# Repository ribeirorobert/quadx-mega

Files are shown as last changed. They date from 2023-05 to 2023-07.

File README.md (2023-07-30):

# Quadx-Mega: Quadricoptero com Arduino (Quadcopter with Arduino)
QuadX-Mega é um quadricoptero desenvolvido com um microcontrolador Arduino Mega Pro mini. O objetivo desse repositório é apresentar de forma simples o hardware e software necessários para a construção de um drone caseiro. A descrição desse projeto tem como base o trabalho de Joop Brokking e totalmente sem fins lucrativos.

Esse projeto destinado a pessoas que gostam de programação, eletrônica, drones, hobbistas e entusiasta de aeromodelos e aviação. Em caso de dúvidas podem entrar em contato direto pelo GitHub ou através do e-mail: robertribeiro100@gmail.com. 

Site do Joop Brokking: http://www.brokking.net/.

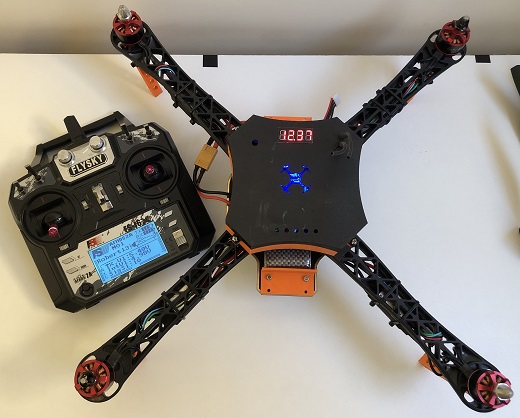
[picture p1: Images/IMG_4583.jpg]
|  | 
|:--:| 
| **Fig. 1** *QuadX-Mega* |

<!-- ![image](https://github.com/ribeirorobert/quadx-mega/edit/feature/altitude-hold/Images/IMG_4565.jpg) -->

# Hardware
A seguir é listado os componentes e peças utilizadas para a construção do quadricoptero. Entretanto, fica a critério e responsabilidade de quem está construindo escolher os itens que irão compor o projeto. Ainda, reforço que nem todos esses componentes são os melhores e mais indicados do mercado, não sendo objetivo construir um drone com melhor preço, com voos a longas distâncias tão pouco a análise da capacidade de carga e duração de voo.

* 1x Frame F450.
* 4x Motor Brushless ReadyToSky 2212 920KV.
* 4x ESC de 30A SimonK.
* 4x Hélice 10x4.5 (2cw e 2 ccw).
* 1x Bateria de Lipo 3S ou 4S com capacidade maior ou igual a 3000mAh. 
* 1x Carregador de bateria Lipo.
* 1x Indicador e alarme de bateria (opcional)
* 1x Radio controle com no mínimo 6 canais. 
* 1x Arduino Mega Pro mini.
* 1x Módulo MPU6050 -> Acelerômetro e Giroscópio 
* 1x Módulo HMC5883L -> Magnetômetro (opcional)
* 1x Módulo MS5611 -> Sensor de pressão barométrica (opcional)
* 1x Módulo GPS NEO 6MV2 (opcional)
* 1x Módulo de comunicação RF Xbee, Lora, NRF24L01 ou APC220 (opcional)
* 1x Buzzer 5V
* 1x LED vermelho
* 1x LED verde
* 1x LED amarelo
* 1x Balanceador de hélice
* 1x Cinta para fixar bateria (opcional)

Observações: 
1. Os motores utilizados possuem furação de fixação em conformidade com o frame. Se optar por utilizar outro conjunto, verifique se a fixação dos motores é coerente com a do frame. 
2. KV: constante de velocidade (para cada 1V de tensão de alimentação há um incremento teórico da velocidade de 920 rpm).
3. Os ESC's utilizados suportam baterias de 2S a 4S.
4. A escolha da hélice tem relação com o tipo de drone que se deseja construir. Algumas são para aplicações onde a prioridade é velocidade. Por outro lado há hélices que são para aplicações onde o peso é o mais importante. Hélices do modelo 10x4.5 são muito comuns e estão no meio termo entre velocidade-peso.
5. O indicador de alarme da bateria é muito útil principalmente para quem está aprendendo a controlar drones/aeromodelos e aqueles que ainda não possuem telemetria integrado. É emitido um alarme sonoro quando a tensão da bateria chega a tensão de limiar pré-definida. O QuadX-Mega possui uma lógica para emitir alarme quando a tensão da bateria atingir 10.7V. Em geral, é definido uma tensão de descarga mínima para cada célula da bateria para garantir sua vida útil. Descargas profundas reduzem a vida útil da bateria. Para o QuadX-Mega a tensão de descarga mínima por célula é de 3,5V com acréscimo de 0,2V como margem de segurança. Em situações em que o quadricoptero esteja a uma distância considerável do operador é aconselhável ter um pouco mais de energia para ganrantir o retorno de forma segura.
6. Em geral um rádio de apenas 4 canais (Roll-CH1, Pitch-CH2, Yaw-CH4 e Throttle-CH3) é suficiente para controlar um drone simples. Entretando, quanto maior o número de canais mais configurações e comandos podem ser adicionados.
7. A escolha do Arduino Mega Pro mini é em função da quantidade de I/Os e tamanho. Outros microcontroladores como Arduino UNO, Arduino Nano, ESP32 ou STM32F103 poderiam ser utilizados tomando os devidos cuidados e modificações pertinentes a cada sistema.
8. O módulo MPU6050 foi utilizado devido a sua qualidade. Existem diversos modelos de acelerômetros disponível no mercado e alguns com mais graus de liberdade (DOFs) como de exemplo o MPU9250 que é um módulo com 9DOFs (acelerômetro, giroscópio e bússola).
9. A PCI (Placa de Circuito Impresso) projetada permite a utilização de diversos sensores e módulos. São eles: MPU6050, MPU9250, BMP180 ou BMP085, HMC5883L, MS5611, GPS NEO-6MV2 e módulos para telemetria via comunicação serial.

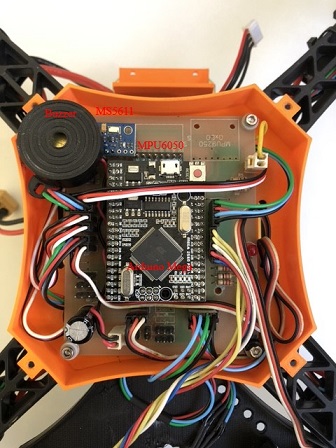
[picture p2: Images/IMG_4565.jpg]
|    | 
|:--:| 
| **Fig. 2** *Eletrônica do quadricoptero* |

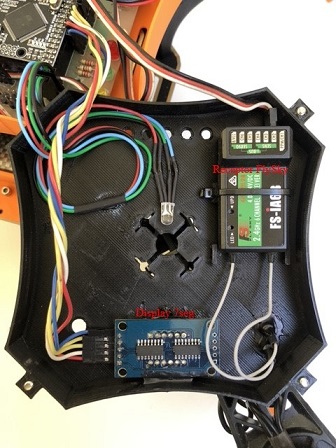
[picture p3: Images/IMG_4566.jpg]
|    | 
|:--:| 
| **Fig. 3** *Eletrônica do quadricoptero* |

O esquemático, lista de componentes e o arquivo Gerber da PCI estão na [pasta PCI](https://github.com/ribeirorobert/quadx-mega/tree/main/PCI) do repositório. 

# Arquivos .STL (STL Files)
Os arquivos .STL utilizados no projeto podem ser acessados diretamente na pasta [STL_files](https://github.com/ribeirorobert/quadx-mega/tree/main/STL_files) do repositório. São eles:
* Skid do trem de pouso.
* Suporte para bateria.
* Case principal.

Observações: 
Foram utilizados peças de fabricação em impressora 3D, mas a confecção desses itens não é obrigatória. Assim, fica a critério do hobbista posicionar certos itens. 

1. Na maioria dos casos o frame do F450 acompanha o skid do trem de pouso principal. Porém, o drone fica um pouco alto (na minha opnião) e em muitas situações fica instável no pouso e decolagem. E como resultado muitas hélices acabam quebrando nessas situações. 
2. A cinta para fixar a bateria é uma opção alternativa. 
3. A case principal foi projetada com objetivo de ser a menor e mais leve possível garantindo a proteção dos componentes da PCI.  

# Software
O código foi desenvolvido em C++ no VScode. Para realizar o download click no botão "<>Code" em verde -> Download ZIP. Ou se preferir basta usar o comando de clone através do git: git clone https://github.com/ribeirorobert/quadx-mega.git que será criado uma cópia do repositório.

O código tem tamanho relativamente grande. Alguns rotinas e funções importantes serão descritas a seguir.

### Defines
Os defines são utilizados para deixar o código mais limpo e organizado além de possibilidar uma maior dinâmica do que está ou não habilitado (flags). Algumas constantes foram definidas com base no datasheet e dados técnicos dos sensores, por outro lado algumas contantes foram obtidas em referência ao trabalho de Joop Brokking ou de forma empírica. Ao mudar alguma constante ou flag tenha certeza do que está fazendo.

As flags a seguir têm função de: habilitar a função de telemetria (se utilizada), habilitar a portal serial do Arduino (para debug), habilitar a rotina com diversas telas de debug, habilitar funções do sensor BMP180 ou MS5611, habilitar a rotina de Fail Safe se implementada, respectivamente. 

```
#define TELEMETRY_ENABLE    0
#define SERIAL_ENABLE       0
#define PRINTF_ENABLE       0
#define BMP180_ENABLE       0
#define MS5611_ENABLE       1
#define FAIL_SAFE           0
```

Já as flags a seguir tem função de habilitar o debug de verificação dos sensores na inicialização do quadricoptero, debug da EEPROM, debug da calibração da IMU, debug da calibração dos ESC's.

```
#define DEBUG_STATUS        0
#define DEBUG_EEPROM        0
#define DEBUG_MPU           0
#define DEBUG_ESC           0
```

### Variáveis
As variáveis em sua maioria são para armazenar os dados dos sensores, controle PID dos ângulo de rolagem (Roll), arfagem (Pitch) e guinada (Yaw), tensão da bateria e status do quadricoptero de modo geral.

### Setup
O setup é função responsável por definir quais pinos do microcontrolador serão definidos como entrada ou saída, inicializar as portas de comunicação Serial e I2C, configurar os pinos de PWM (Pulse Width Modulation) dos ESC's, verificar se os sensores habilitados estão respondendo corretamente e atualizar os timers utilizados no código.

### Loop
É a função principal do código e todas as demais rotinas serão chaveadas de maneira sequencial. É importante destacar que o loop "roda" a uma taxa de 250 Hz (4ms). Esse valor foi definido em conformidade com a frequência de operação dos ESC's. Assim, todas as demais rotinas de controle e leitura dos sensores estão sendo executadas nessa velocidade. Em alguns casos expecíficos como de exemplo da aquisição dos dados do sensor de pressão barométrica foram criados artifícios para escalonar essa taxa. As funções executadas dentro do loop são descritas a seguir.

1. acc_gyro_values(): Essa rotina é responsável por aquisitar os bytes do registradores do acelerômetro e giroscópio do sensor MPU6050 e ainda subtrair dos valores de calibração.

2. euler_angles(): É responsável por filtrar os dados obtidos na função anterior e computar os ângulos de Roll e Pitch através das Equações de Euler. 

Para mais informações visite: 
- https://www.youtube.com/watch?v=pQ24NtnaLl8 
- https://en.wikipedia.org/wiki/Euler_angles
- https://www.youtube.com/watch?v=5IkPWZjUQlw&t=17s
- https://www.youtube.com/watch?v=nCPEJTUYch8&t=616s
- https://www.youtube.com/watch?v=j-kE0AMEWy4&t=9s

3. read_radio_commands(): Essa função é responsável por interpretar alguns comandos combinados do rádio.
* Ligar/Desligar os motores

O status dos motores é divido em três categorias, são elas: LOCK, IDLE e FULL. No status de LOCK os motores permanecem desligados. Já no status de IDLE os motores são acionados em rotação mínima e por fim em FULL os motores podem assumir rotação entre minimo e máximo de acordo com a posição do stick de throttle do radio controle. O objetivo dessa implementação é evitar de modo não intencional os motores sejam acionados. Lembrando que motores brushless operam em rotações elevadas e com a hélice conectada tornam-se perigosos.

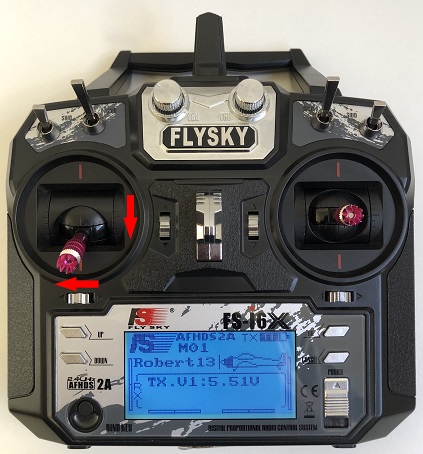
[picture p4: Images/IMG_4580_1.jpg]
|    | 
|:--:| 
| **Fig. 4** *Comando para ligar os motores* |

Seguindo a indicação das setas mostrado na Figura acima, uma primeira tentativa o status dos motores em LOCK muda para IDLE e um segunda tentativa os motores mudam para o status de FULL, ou seja, aceleração desbroqueada. Para desligar basta seguir a instrução da Figura 5.

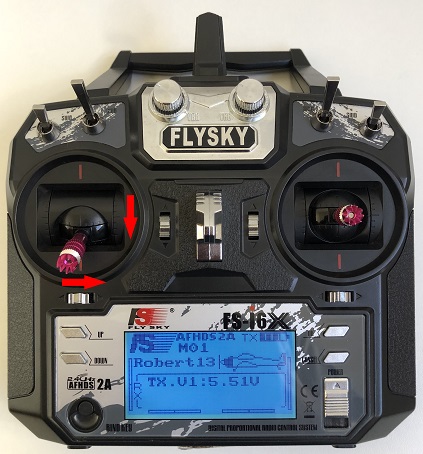
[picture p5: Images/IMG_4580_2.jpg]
|    | 
|:--:| 
| **Fig. 5** *Comando para desligar os motores* |

* Calibrar IMU -> Giroscópio

Da mesma forma para calibrar o giroscópio é preciso executar a instrução indicada em vermelho duas vezes. Caso queira cancelar a calibração, basta executar a indicação em azul (Figura 10).

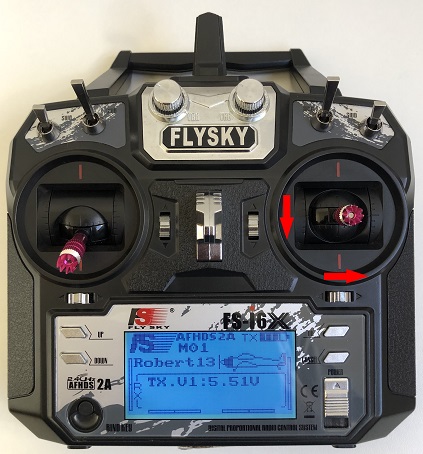
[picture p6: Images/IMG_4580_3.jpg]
|    | 
|:--:| 
| **Fig. 6** *Comando calibrar o giroscópio* |

* Calibrar IMU -> Acelerômetro

Para calibrar o acelerômetro é preciso executar a instrução indicada em vermelho duas vezes. Caso queira cancelar a calibração, basta executar a indicação em azul (Figura 10).

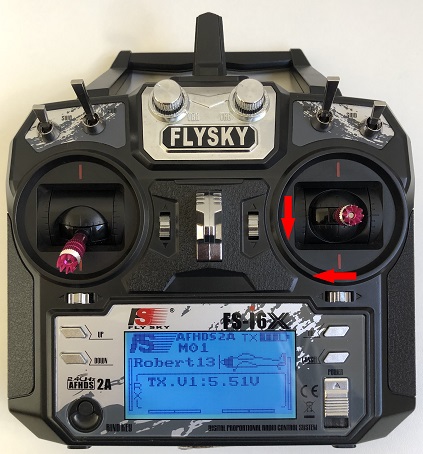
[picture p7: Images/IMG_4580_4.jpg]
|    | 
|:--:| 
| **Fig. 8** *Comando para calibrar o acelerômetro* |

* Calibrar os ESC's

Para calibrar os ESC's é preciso executar a instrução indicada em vermelho duas vezes (Figura 9). Caso queira cancelar a calibração, basta executar a indicação em azul (Figura 10). Porém, a calibração dos ESC's possui um terceira etapa da seguinte forma: 

- Desconecte a bateria e mova o stick do throttle para a posição máxima. 
- Conecte a bateria novamente e aguarde o beep dos motores.
- Mova o stick do throttle para a posição mínima e aguarde o beep dos motores novamente. 
    
Tudo executado corretamente basta realizar o comando para sair da calibração (Figura 10). Se esse comando não for executado ao fim da calibração, toda vez que o drone for ligado a rotina de calibração dos ESC's será executada primeiro.

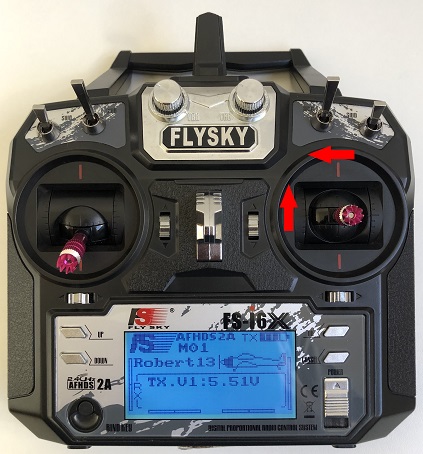
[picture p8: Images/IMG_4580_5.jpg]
|    | 
|:--:| 
| **Fig. 9** *Comando para calibrar os ESC's* |

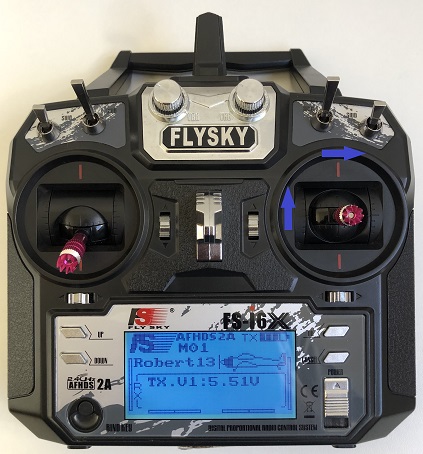
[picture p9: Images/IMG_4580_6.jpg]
|    | 
|:--:| 
| **Fig. 10** *Comando para cancelar* |

* Habilitar Altitude Hold (em desenvolvimento)

Quando habilitada a rotina de Altitude Hold possibilita com o que o quadricoptero permanace em uma altitude fixa usando como referência a pressão barométrica. Ao mover o stick de throttle essa referência de altitude é atualizada até que o stick retorne a posição central. 

Para mais informações da implementação visite: 
- https://www.youtube.com/watch?v=2BLb6qUKikI&t=702s

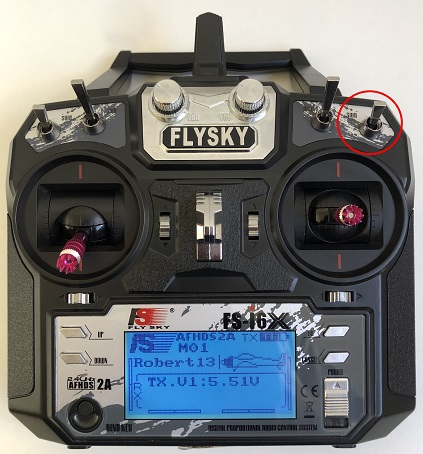
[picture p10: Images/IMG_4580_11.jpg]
|    | 
|:--:| 
| **Fig. 11** *Hibilitar o Altitude Hold* |

* Ligar/Desligar LEDs do frame

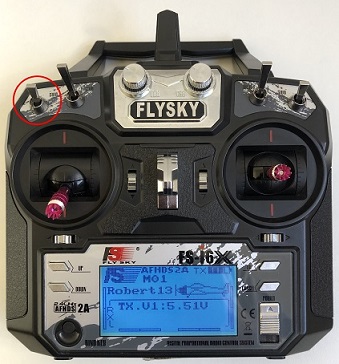
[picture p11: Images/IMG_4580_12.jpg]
|    | 
|:--:| 
| **Fig. 12** *Acionar os LEDs do frame* |

Observações: Algumas rotinas possuem um timeout, ou seja, ao selecionar uma calibração mas não confirmar, após um intervalo de tempo de 2 minutos a instrução será cancelada. Ainda, para habilitar a calibração do acelerômetro, giroscópio e ESC's o status dos motores deve necessarimente ser LOCK, ou seja, só é possível acionar essas funções com os motores desligados. Há um display de 7 segmentos para auxiliar de maneira visual com as instruções. Em caso de erro de calibração uma mensagem será exibida na tela e bloqueado para voo. Nessa situação desconecte a bateria e realize o procedimento novamente. 

IMPORTANTE: sempre que for calibrar a IMU (Inertial Measurement Unit) certifique-se que o quadricoptero está sobre uma superfície plana, do contrário, o mesmo pode voar com um pouco de inclinação ou apresentar a mensagem de erro na etapa de calibração. Os valores de calibração da IMU são armazenados na EEPROM. Se o quadricoptero não sofrer queda ou impacto não há necessidade de qualibrar a IMU e os ESC's sempre que for ligado.

4. execute_pid_controllers(): Essa função é responsável por executar o controle dos três ângulos (Roll, Pitch e Yaw). Foi utilizado o famoso controlador PID (Proporcional-Integral-Derivativo), porém não será o foco aqui descrever como esse controlador funciona e como projetar os ganhos Kp, Ki e Kd, respectivamente. Cada ângulo possui uma referência que são as respectivas posições dos stick de cada movimento. A referência dos stick são comparadas com os Ângulos de Euler calculados para gerar o sinal de erro, esse por último sendo o objeto de rastreamento e minimização do algoritimo PID. Foi implementando uma rotina para criar uma zona morta (dead band) do sinal de referência dos sticks com intuito de manter nulo o sinal de referência para oscilações mínimas do seu movimento. Essa função "retorna" três sinais de controle que serão utilizados para aumentar/reduzir a rotação dos motores de modo a transformar essas rotações em uma postura/movimento (Attitude) do quadricoptero. 

5. read_battery_voltage(): Essa função é responsável pela leitura da tensão da bateria e filtragem.
6. show_quad_status(): Essa rotina é responsável por mostrar as mensagem e valor da tensão na bateria no display de 7 segmentos.
7. check_alarms(): Essa função é encarregada de acionar os LED's de notificação, buzzer para nível crítico de bateria e LED's do frame.

8. esc_pwm_signals(): Função responsável por atribuir as respectivas velocidades de rotação a cada motor de acordo com a configuração de "X" do quadricoptero. Existem diversas configurações para distribuir o comando de throttle e sinal de controle PID(Roll, Pitch, Yaw) para os motores, cada um com particularidades, vantagens e desvantagens. Cada aplicação terá um ou mais conjunto de configurações recomendáveis. Nesse projeto a distribuição utilizada é dada por:

```
esc1 = throttle - pidPitch + pidRoll - pidYaw); //PWM for ESC 1, front-right - CCW
esc2 = throttle + pidPitch + pidRoll + pidYaw); //PWM for ESC 2, rear-right  - CW
esc3 = throttle + pidPitch - pidRoll - pidYaw); //PWM for ESC 3, rear-left   - CCW
esc4 = throttle - pidPitch - pidRoll + pidYaw); //PWM for ESC 4, front-left  - CW
 ```

9. print_info(): Rotina exclusiva para debug de variáveis. 

IMPORTANTE: manter a flag PRINTF_ENABLE 0 quando for voar com o quadricoptero.

10. ISR(PCINT0_vect): Essa rotina não é executada no Loop, mas é muito importante pois é responsável pela leitura dos sinais PPM (Pulse Position Modulation) do rádio controle. A vantagem em utilizar o modo PPM é a redução da quantidade de fios necessários para aquisitar os pulsos de cada canal. Alguns rádios possuem apenas a opção de PWM, assim, cada canal fornece de forma independente um pulso com largura de 1000-2000us (4º link). O rádio utilizado no projeto é o FlySky FS-I6X, com 6 canais por padrão mas pode ser atualizado para trabalhar com 10 canais juntamente com um recepetor para 10 canais. No modo PPM é possível utilizar 8 canais com o receptor original.

Este vídeo mostra o passo a passo da calibração da IMU e acionamento dos motores: https://drive.google.com/file/d/1GBvPZ2bElnIvH8ivOGOF917iYf-E5jJ1/view?usp=sharing

Para mais informações visite: 
- https://www.youtube.com/watch?v=lxE4K7ghST0&list=PLDnffNsiQx6PM4rRNhtB-s_rc2s0CCEmk
- https://www.youtube.com/watch?v=63JmO4Mc8NM
- https://www.youtube.com/watch?v=IsxJD7lS0Go
- http://electronoobs.com/eng_robotica_tut9_1.php

# Montagem (The build)
A Figura 13 mostra em detalhes o sentido de giro de cada motor.
* Motor 1: frontal direito
* Motor 2: traseiro direito
* Motor 3: traseiro esquerdo
* Motor 4: frontal esquerdo

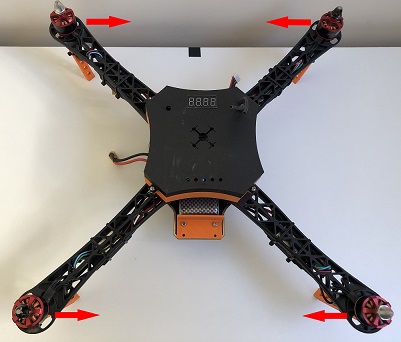
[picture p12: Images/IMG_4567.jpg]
|    | 
|:--:| 
| **Fig. 13** *Acionar os LEDs do frame* |

Os motores 1 e 3 rodam no sentido antihorário e os motores 2 e 4 por consequência no sentido horário. Se ao acionar os motores algum esteja girando no sentido contrário, basta trocar dois fios conectados ao ESC do respectivo motor para modificar o sentido de giro. IMPORTANTE: sempre teste o sentido de giro dos motores antes de conectar as hélices. 

A Figura 14 mostra com detalhes o bordo de ataque, o dorso, bordo de fuga e face de uma hélice. 

|    | 
|:--:| 
| **Fig. 14** *Acionar os LEDs do frame [3](https://formacaopiloto.blogspot.com/2014/09/aeronaves-e-motores-capitulo-xiv-helices.html)* |

Assim, o bordo de ataque da hélice deve girar no mesmo sentido que as setas em vermelho da Figura 13. Para mais detalhes da montagem acesse a pasta de [Imagens](https://github.com/ribeirorobert/quadx-mega/tree/main/Images) no repositório.

# Trabalhos Futuros (Future Works)
Algumas implementações ainda estão em backlog, em breve serão disponibilizados rotinas tais como:
* Altitude Hold
* GPS Hold and Route Track
* Back-to-Home
* Telemetry

# Referências (References)
[1] Brokking.net. Link: http://www.brokking.net/

[2] Youtube Joop Brokking. Link: https://www.youtube.com/@Joop_Brokking

[3] Capítulo XIV: Hélices. Formação de Piloto. Link: https://formacaopiloto.blogspot.com/2014/09/aeronaves-e-motores-capitulo-xiv-helices.html

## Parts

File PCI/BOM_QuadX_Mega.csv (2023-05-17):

ID | Name | Designator | Footprint | Quantity
1 | Bateria | J21 | HDR-M-2.54_1X2 | 1
2 | 1000u | C1 | CAP-D10.0-F5.0 | 1
3 | GPS | J20 | HDR-M-2.54_1X4 | 1
4 | TELEMETRIA | J1 | HDR-M-2.54_1X4 | 1
5 | GSM | J11 | HDR-M-2.54_1X4 | 1
6 | RADIO_PPM1 | J2 | HDR-M-2.54_1X3 | 1
7 | RADIO_PPM2 | J3 | HDR-M-2.54_1X3 | 1
8 | RADIO_PPM3 | J4 | HDR-M-2.54_1X3 | 1
9 | PWM_AUX | J6,J7 | HDR-M-2.54_1X3 | 2
10 | HDR-M-2.54_1x3 | J12,J13,J14,J15,J16,J17,J18,J19 | HDR-M-2.54_1X3 | 8
11 | RADIO_PWM | J5 | HDR-M-2.54_1X8 | 1
12 | BUZZER | J8 | HDR-M-2.54_1X2 | 1
13 | POWER_AUX | J9,J10 | HDR-M-2.54_1X2 | 2
14 | ARDUINO MEGA2560 MINI PRO | U1 | ARDUINO MEGA2560 MINI PRO | 1
15 | GY521_MPU6050 | U3 | GY521MPU6050 | 1
16 | GY-271 | U4 | HMC5883L_GY271_MODULE | 1
17 | 100 | R1,R2,R3 | R_AXIAL-0.4 | 3
18 | 10k | R4,R5 | R_AXIAL-0.4 | 2
19 | 4k7 | R6 | R_AXIAL-0.4 | 1
20 | 5mm | LED1,LED2,LED3 | LED-TH_BD5.8-P2.54-FD | 3
21 | K4 | KEY1 | KEY-TH_4P-L6.0-W6.0-P4.50-LS6.5 | 1

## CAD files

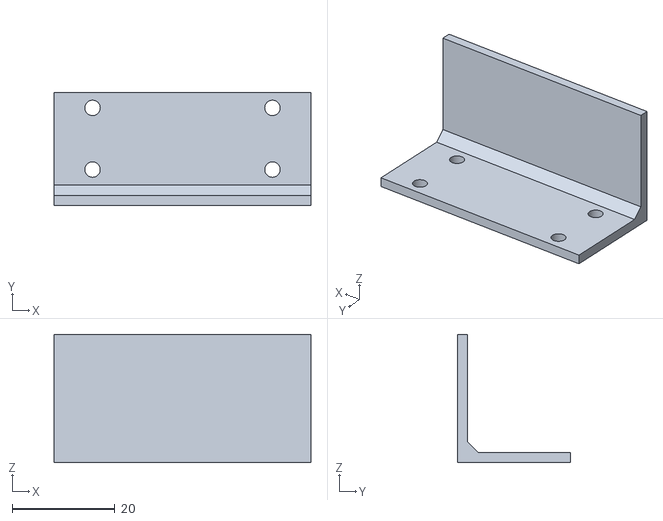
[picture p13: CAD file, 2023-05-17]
STL_files/2x_Battery_holder.stl
50.0 x 22.0 x 25.0

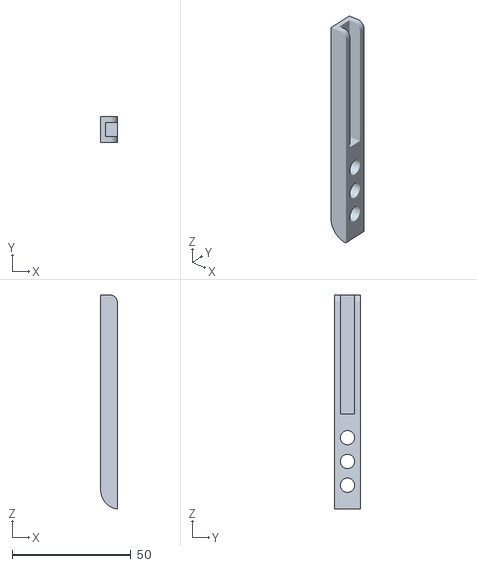
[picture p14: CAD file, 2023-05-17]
STL_files/4x_Skid_landing_gear.stl
7.00 x 11.0 x 90.0

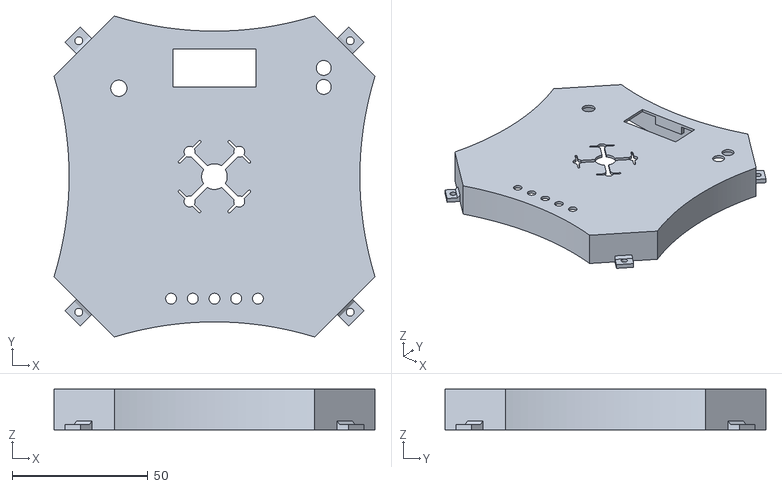
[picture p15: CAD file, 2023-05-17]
STL_files/1x_Case_top.stl
118.3 x 118.3 x 15.0

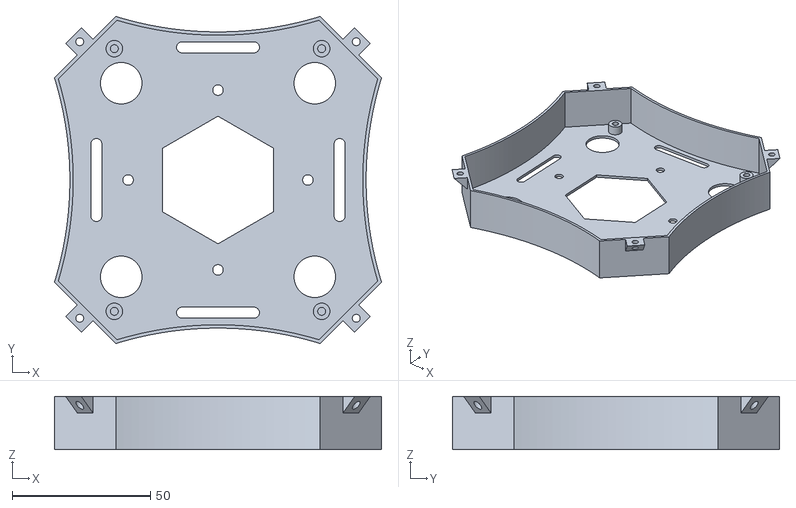
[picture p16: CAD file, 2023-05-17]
STL_files/1x_Case_bottom.stl
118.3 x 118.3 x 19.2

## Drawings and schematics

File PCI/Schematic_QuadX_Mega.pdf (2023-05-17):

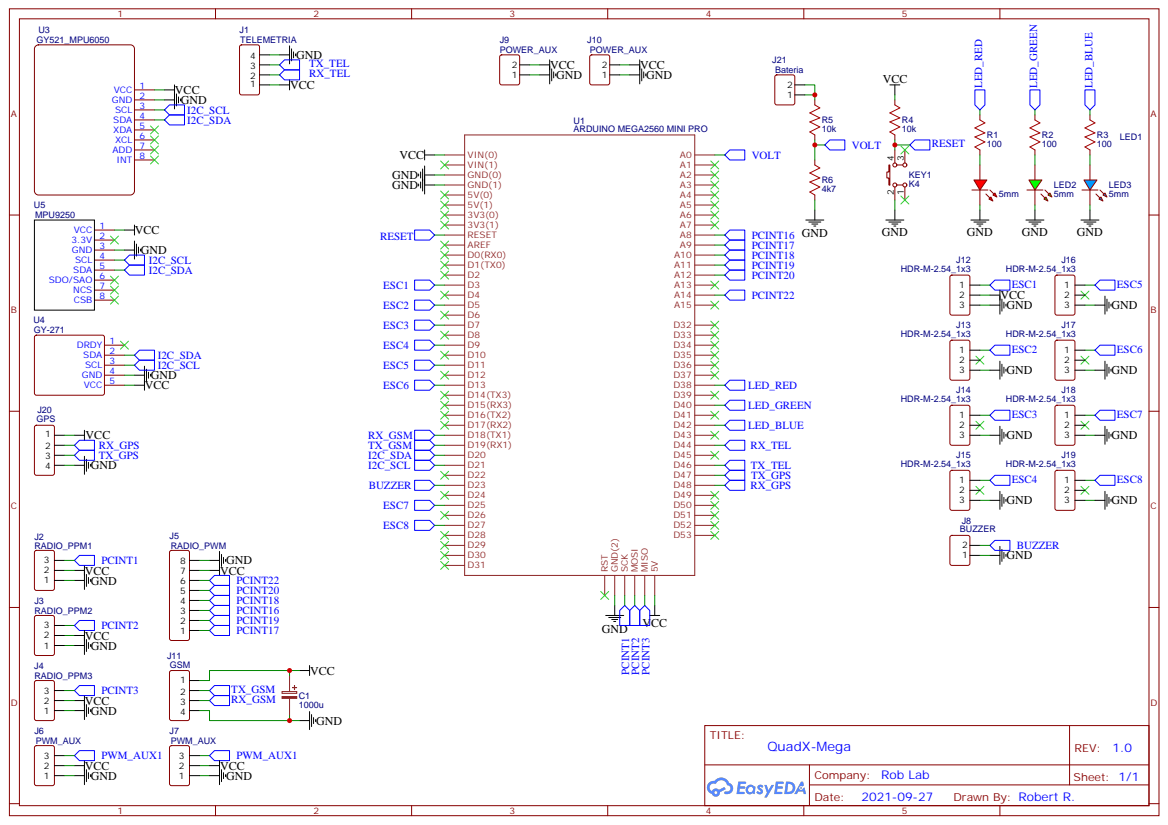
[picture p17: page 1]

VCC GNDPCINT¹ PCINT² PCINT³

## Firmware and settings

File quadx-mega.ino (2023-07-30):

/*    
  QuadX Mega - v1.0.
  Created by Robert R. Gomes, May 17, 2023. 
  All rights reserved.
*/

#include <EEPROM.h>
#include <Wire.h>

#define SERIAL_BAUD_RATE    38400UL
#define I2C_CLOCK_SPEED     400000UL
#define I2C_TIMEOUT         4000UL

#define serialXBEE          Serial1   

#define TELEMETRY_ENABLE    0
#define SERIAL_ENABLE       0
#define PRINTF_ENABLE       0
#define BMP180_ENABLE       0
#define MS5611_ENABLE       1
#define FAIL_SAFE           0

#define DEBUG_STATUS        0
#define DEBUG_EEPROM        0
#define DEBUG_MPU           0
#define DEBUG_ESC           0

//#define BMP180
#define MS561101BA

#define MPU6050_ADDRESS     0x68
#define COMPASS_ADDRESS     0x1E
#define BMP180_ADDRESS      0x77
#define MS5611_ADDRESS      0x77
#define GYRO_ADDRESS        0x69
#define ACC_ADDRESS         0x53

#define LED_FRONT_LEFT      5
#define LED_FRONT_RIGHT     62
#define LED_REAR_LEFT       11
#define LED_REAR_RIGHT      48
#define VIRTUAL_GND         63

#define LED_YELLOW_PIN      42
#define LED_GREEN_PIN       40
#define LED_BLUE_PIN        44
#define LED_RED_PIN         38
#define BUZZER_PIN          23

#define BATTERY_PIN         A0
#define CLOCK_PIN           A14
#define LATCH_PIN           A10
#define DATA_PIN            A12 

#define WAITING_SAFETY_PERIOD       120000UL
#define CHANNEL_READ_PERIOD         100000UL
#define READ_BATTERY_PERIOD         2000000UL
#define IGNORE_CMDS_PERIOD          1000000UL
#define PWM_SAFETY_PERIOD           2100UL
#define TELEMETRY_PERIOD            1000000UL
#define BLINK_LED_PERIOD            1000000UL
#define CTRL_LOOP_PERIOD            4000UL
#define DISP_7SEG_PERIOD            4000UL
#define BUZZER_PERIOD               1000000UL
#define LEDS_PERIOD                 500000UL

#define MAX_RUNNING_TIME            900000UL

#define SENSITIVITY_SCALE_FACTOR    0.015267F //0.015267 = 1/65.5 [º/s]
#define BATTERY_UPPER_THRESHOLD     10.7F
#define BATTERY_LOWER_THRESHOLD     6.0F
#define BATTERY_COMPENSATION        0.000571F //1/3500
#define LEVEL_ADJUST_FACTOR         15.0F
#define DEGREES_TO_RADIAN           0.000001066F //0.000001066 = 0.0000611*(PI/180)
#define RADIAN_TO_DEGREES           57.295779F //57.295779 = 180/PI
#define ZERO_RATE_OUTPUT            0.0000611F //0.0000611 = 1/(250Hz/65.5) [º]
#define VOLTAGE_FACTOR              0.015285F //R2/R1+R2 = K = 0.319727, (5.0/1023) / K = 0.015285
#define HALF_LOOP_RATE              0.002F //sample time / 2

#define FAILSAFE_THRESHOLD          990
#define AUTO_LEVEL_MODE             1

#define QUADX_STATUS_UNDEFINED      0b00000000  
#define QUADX_RADIO_STARTUP_FAIL    0b00000001
#define QUADX_ESC_NOT_CALIBRATED    0b00000010
#define QUADX_EEPROM_READ_FAIL      0b00000100 
#define QUADX_GYRO_CALIBRATED       0b00001000
#define QUADX_ACC_CALIBRATED        0b00010000
#define QUADX_MPU6050_ERROR         0b00100000
#define QUADX_BMP180_ERROR          0b01000000
#define QUADX_MS5611_ERROR          0b01000000
#define QUADX_STATUS_OK             0b10000000

#if defined(BMP180)
#define BMP180_READ_TEMPERATURE     0x2E
#define BMP180_TEMPERATURE_DATA     0xF6
#define BMP180_READ_PRESSURE        0x34
#define BMP180_PRESSURE_DATA        0xF6
#define BMP180_AC1_ADDRESS          0xAA
#define BMP180_CONTROL              0xF4
#define BMP180_OSS                  0x03

#define BMP180_WAIT_UT_READ         6000UL
#define BMP180_WAIT_UP_READ         21000UL
#endif

#if defined(MS561101BA)
#define MS5611_TEMPERATURE_ADDR     0x50
#define MS5611_PRESSURE_ADDR        0x40
#define MS5611_REG_RESET            0x1E
#define MS5611_OSR_4096             0x08

#define MS5611_WAIT_UT_UP_READ      10000UL
#endif

#define GYROX_OFFSET_EEPROM_ADDR    0x00
#define GYROY_OFFSET_EEPROM_ADDR    0x04
#define GYROZ_OFFSET_EEPROM_ADDR    0x08
#define ACCX_OFFSET_EEPROM_ADDR     0x0C
#define ACCY_OFFSET_EEPROM_ADDR     0x10
#define ACCZ_OFFSET_EEPROM_ADDR     0x14
#define ESC_CAL_EEPROM_ADDR         0xFF

#define TEMPERATURE_INDEX     5U
#define PARACHUTE_INDEX       30U
#define ALT_ERROR_INDEX       10U
#define PRESSURE_INDEX        20U

#define GYRO_OFFSET_INDEX     1000UL
#define ACC_OFFSET_INDEX      100U

#define ACCZ_SHORT_INDEX      25U
#define ACCZ_LONG_INDEX       50U
#define ACCZ_THRESHOLD        800UL

#define STICK_MIDPOINT    1500UL
#define STICK_UPPER_DB    1510.0F
#define STICK_LOWER_DB    1490.0F
#define MIN_THROTTLE      1000UL
#define MAX_THROTTLE      1800UL
#define LOCK_SPEED        1000UL   
#define IDLE_SPEED        1200UL 
#define FULL_SPEED        2000UL  

#define LOCK_THROTTLE     0x00
#define IDLE_THROTTLE     0x01
#define FULL_THROTTLE     0x02

#define MAX_PID_OUTPUT    400.0F
#define MAX_STICK_REF     150.0F

#define ALL_LEDS_OFF  0b00000000
#define ALL_LEDS_ON   0b00000001
#define LED_YELLOW    0b00000010
#define LED_GREEN     0b00000100
#define LED_BLUE      0b00001000
#define LED_RED       0b00010000
#define LED_FRONT     0b00100000
#define LED_REAR      0b01000000

// #define KP_ALT_HOLD   1.4
// #define KI_ALT_HOLD   0.2
// #define KD_ALT_HOLD   0.75

#define KP_ALT_HOLD   2.0
#define KI_ALT_HOLD   0.4
#define KD_ALT_HOLD   0.75

#define KP_PITCH      1.2
#define KI_PITCH      0.04
#define KD_PITCH      20.0

#define KP_ROLL       1.2
#define KI_ROLL       0.04
#define KD_ROLL       20.0

#define KP_YAW        4.0
#define KI_YAW        0.02

struct {
  uint8_t status;
  uint8_t motors;
  uint8_t leds;
  bool buzzer;
} quadX;

struct {
  union {int32_t val; uint8_t raw[4];} gyroXOffset;
  union {int32_t val; uint8_t raw[4];} gyroYOffset;
  union {int32_t val; uint8_t raw[4];} gyroZOffset;

  union {int32_t val; uint8_t raw[4];} accXOffset;
  union {int32_t val; uint8_t raw[4];} accYOffset;

  int32_t gyroX;
  int32_t gyroY;
  int32_t gyroZ;

  int16_t temp;

  int32_t accX;
  int32_t accY;
  int32_t accZ;
} MPU6050;

#if defined(BMP180)
struct {
  int16_t ac1;
  int16_t ac2;
  int16_t ac3;
  uint16_t ac4;
  uint16_t ac5;
  uint16_t ac6;
  int16_t b1;
  int16_t b2;
  int16_t mb;
  int16_t mc;
  int16_t md;

  union {
    int16_t val;
    int8_t raw[2];
  } UT;

  union {
    int32_t val;
    int8_t raw[4];
  } UP;

  int32_t temperature;
  int32_t pressure;

  unsigned long timeOut;
  bool status;
} BMP180;
#endif

#if defined(MS561101BA) 
struct {
  uint16_t c[7];

  union {
    int32_t val;
    int8_t raw[4];
  } ut;

  union {
    uint32_t val;
    int8_t raw[4];
  } up;

  int32_t temperature;
  int32_t pressure;

  unsigned long timeOut;
  bool status;
} MS5611;
#endif

const uint8_t numbers[10] = {
  0b00000011, 0b10011111, 0b00100101, 0b00001101, 0b10011001, 
  0b01001001, 0b01000001, 0b00011111, 0b00000001, 0b00001001
};

const uint8_t fail[5] = {
  0b01110001, 0b00010001, 0b10011111, 0b11100011, 0b11111111
};

const uint8_t eeprom[10] = {
  0b01100001, 0b01100001, 0b00110001, 0b11110101, 0b11000101, 
  0b11010101, 0b11111111, 0b11111111, 0b11111111, 0b11111111
};

const uint8_t mpu[11] = {
  0b11010101, 0b00110001, 0b11000111, 0b01000001, 0b00000011, 
  0b01001001, 0b00000011, 0b11111111, 0b11111111, 0b11111111, 
  0b11111111
};

const uint8_t bmp[10] = {
  0b11000001, 0b11010101, 0b00110001, 0b10011111, 0b00000001, 
  0b00000011, 0b11111111, 0b11111111, 0b11111111, 0b11111111
};

const uint8_t ms[11] = {
  0b11010101, 0b01001001, 0b11111111, 0b01001001, 0b01000001, 
  0b10011111, 0b10011111, 0b11111111, 0b11111111, 0b11111111, 
  0b11111111
};

const uint8_t radio[9] = {
  0b11110101, 0b00010001, 0b10000101, 0b11011111, 0b11000101, 
  0b11111111, 0b11111111, 0b11111111, 0b11111111
};

const uint8_t esc[7] = {
  0b01100001, 0b01001001, 0b01100011, 0b11111111, 0b11111111, 
  0b11111111, 0b11111111
};

uint8_t msg[6*sizeof(fail)+sizeof(eeprom)+sizeof(mpu)+sizeof(bmp)+sizeof(ms)+sizeof(radio)+sizeof(esc)];

bool statusCalibrationEsc = false;
bool statusManualAltitude = false;
bool statusAltitudeHold = false;

uint8_t counterFailSafe = 0;
uint8_t debugPageIndex = 1;
uint8_t muxIndex = 0;

volatile uint16_t channel[9];

uint16_t currentThrottle, initialThrottle;
float adjustThrottle;
float manualThrottle;

float batteryVoltage;

//roll, pitch and yaw variables
float gyroRollInput, gyroPitchInput, gyroYawInput;
float rollAngle, pitchAngle;

float rollLevelAdjust, pitchLevelAdjust;
float rollAngleAcc, pitchAngleAcc;

//roll, pitch and yaw ctrl variables
float rollSetPoint, pitchSetPoint, yawSetPoint;

float errorRoll, errorPitch, errorYaw;
float pTermRoll, pTermPitch, pTermYaw;
float iTermRoll, iTermPitch, iTermYaw;
float dTermRoll, dTermPitch, dTermYaw;

float errorRollAnt, errorPitchAnt, errorYawAnt;
float pidRoll, pidPitch, pidYaw;

//altitude hold ctrl variables
float altHoldSetPoint, errorAltHold, pidAltHold;
float pTermAltHold, iTermAltHold, dTermAltHold;

//altitude hold variables
uint8_t altitudeErrorIndex = 0;
uint8_t temperatureIndex = 0;
uint8_t parachuteIndex = 0;
uint8_t pressureIndex = 0;

int32_t rawTemperature;
int32_t parachuteThrottle;

int32_t temperatureSum;
int32_t pressureSum;

int32_t temperatureBuffer[TEMPERATURE_INDEX];
int32_t parachuteBuffer[PARACHUTE_INDEX];
int32_t pressureBuffer[PRESSURE_INDEX];

float altitudeErrorBuffer[ALT_ERROR_INDEX];

float altitudeErrorSum;
float altitudeError;

float actualPressure, groundPressure;
float actualPressureFast, actualPressureSlow;
float actualPressureDiff;

float previousParachutePressure;

//time variables
unsigned long previousReadVoltagePeriod;
unsigned long previousIgnoreCmdsPeriod;
unsigned long previousCtrlLoopPeriod;
unsigned long previousBuzzerPeriod;
unsigned long previousBlinkPeriod;
unsigned long startQuadXTimer;

void setup() {
  //initialize serial
#if SERIAL_ENABLE  
  Serial.begin(SERIAL_BAUD_RATE);
  delay(1000);
#endif

#if TELEMETRY_ENABLE
  serialXBEE.begin(9600); //Rx, Tx
#endif

  //initialize I2C
  Wire.begin();
  Wire.setClock(I2C_CLOCK_SPEED); //TWBR = 12; set the I2C clock speed to 400kHz

  //inputs and outputs
  pinMode(BATTERY_PIN, INPUT);

  pinMode(LED_FRONT_LEFT,  OUTPUT);
  pinMode(LED_FRONT_RIGHT, OUTPUT);
  pinMode(LED_REAR_LEFT,   OUTPUT);
  pinMode(LED_REAR_RIGHT,  OUTPUT);
  pinMode(VIRTUAL_GND,     OUTPUT);

  pinMode(LED_YELLOW_PIN, OUTPUT);
  pinMode(LED_GREEN_PIN,  OUTPUT); 
  pinMode(LED_BLUE_PIN,   OUTPUT); 
  pinMode(LED_RED_PIN,    OUTPUT);
  pinMode(BUZZER_PIN,     OUTPUT);
  
  pinMode(CLOCK_PIN, OUTPUT);
  pinMode(LATCH_PIN, OUTPUT);
  pinMode(DATA_PIN,  OUTPUT);

  //virtual GND
  digitalWrite(VIRTUAL_GND, LOW);

  DDRE |= bit(DDE5); //data direction register PORTE.5 (ESC1)
  DDRB |= bit(DDB7); //data direction register PORTB.7 (ESC2)

  DDRH |= bit(DDH4); //data direction register PORTH.4 (ESC3)
  DDRH |= bit(DDH6); //data direction register PORTH.6 (ESC4)

  PCMSK0 |= bit(PCINT2); //want pin B2
  PCIFR |= bit(PCIF0); //clear any outstanding interrupts
  PCICR |= bit(PCIE0); //enable pin change interrupts PCMSK0

  //blink LEDs
  blink_leds();

  //quadX status
  quadX_status();

  //get battery voltage
  batteryVoltage = analogRead(BATTERY_PIN) * VOLTAGE_FACTOR;

  //update timers
  previousReadVoltagePeriod = micros();
  previousIgnoreCmdsPeriod = micros();
  previousCtrlLoopPeriod = micros();
  previousBuzzerPeriod = micros();
  previousBlinkPeriod = micros();
  startQuadXTimer = millis();
}

void loop() {
  //reading accelerometer and gyroscope angles
  acc_gyro_values();

  //accelerometer and gyroscope euler angles
  euler_angles();

  //read commands from radio   
  read_radio_commands();

  //read pressure and temperature
#if BMP180_ENABLE    
  BMP180_update();
#endif  

#if MS5611_ENABLE    
  //MS5611_update();
#endif  

  //altitude hold
#if MS5611_ENABLE  
  altitude_hold(3);
#endif  

  //roll, pitch and yaw PIDs controllers
  execute_pid_controllers();

  //read battery voltage
  read_battery_voltage();

  //show on display quadX status
  show_quad_status();

  //check alarms
  check_alarms();

  //ctrl loop period
  while (micros() - previousCtrlLoopPeriod < CTRL_LOOP_PERIOD);
  previousCtrlLoopPeriod = micros();

  //ESCs PWM signals
  esc_pwm_signals();  

  //print data on serial monitor debugPageIndex
#if PRINTF_ENABLE
  print_info(7);
#endif

  //telemetry parameters
#if TELEMETRY_ENABLE
  update_telemetry_parameters();
#endif
}

/*******************************************************
  quadX status
/*******************************************************/
void quadX_status(void) {
#if DEBUG_STATUS
  Serial.println(F("QUADX STARTING..."));
#endif

  //quadX default status
  quadX.status |= QUADX_STATUS_UNDEFINED;
  quadX.motors = LOCK_THROTTLE;
  quadX.leds = ALL_LEDS_OFF;
  quadX.buzzer = false;

  //read EEPROM data
#if DEBUG_STATUS
  Serial.print(F("->READING EEPROM: "));
#endif
  
  if (!read_eeprom()) {
#if DEBUG_STATUS
    Serial.println(F("ERROR"));
#endif
    quadX.status |= QUADX_EEPROM_READ_FAIL;
    fail_message();
  } else {
#if DEBUG_STATUS
    Serial.println(F("OK"));
#endif
    quadX.status |= QUADX_GYRO_CALIBRATED;
    quadX.status |= QUADX_ACC_CALIBRATED;
  }

  //ESCs calibration
#if DEBUG_STATUS
  Serial.print(F("->ESC CALIBRATION: "));
#endif

  if (statusCalibrationEsc) {
    if (!esc_calibration_signals()) {
#if DEBUG_STATUS
      Serial.println(F("ERROR"));
#endif
      quadX.status |= QUADX_ESC_NOT_CALIBRATED;
    } else {
#if DEBUG_STATUS
      Serial.println(F("OK"));
#endif
    }

    EEPROM.write(ESC_CAL_EEPROM_ADDR, 0);
  } else {
#if DEBUG_STATUS
    Serial.println(F("SKIPED"));
#endif
  }

  //check if MPU6050 is ok
#if DEBUG_STATUS
  Serial.print(F("->CHECKING MPU6050: "));
#endif
  
  for (uint8_t i = 0; i < 10; i ++) {
    Wire.beginTransmission(MPU6050_ADDRESS);
    uint8_t status = Wire.endTransmission();

    if (status != 0) {
#if DEBUG_STATUS
      Serial.println(F("ERROR"));
#endif
      quadX.status |= QUADX_MPU6050_ERROR;
    } else {
#if DEBUG_STATUS
      Serial.println(F("OK"));
#endif
      MPU6050_init(); //IMU configuration
      quadX.status &= ~QUADX_MPU6050_ERROR;
      break;
    }
    delay(500);
  }

  //check if BMP180 is ok
#if defined(BMP180)  
#if DEBUG_STATUS
  Serial.print(F("->CHECKING BMP180: "));
#endif

  for (uint8_t i = 0; i < 10; i ++) {
    Wire.beginTransmission(BMP180_ADDRESS);
    uint8_t status = Wire.endTransmission();

    if (status != 0) {
#if DEBUG_STATUS
      Serial.println(F("ERROR"));
#endif
      quadX.status |= QUADX_BMP180_ERROR;
    } else {
#if DEBUG_STATUS
      Serial.println(F("OK"));
#endif      
      BMP180_init();
      quadX.status &= ~QUADX_BMP180_ERROR;
      break;
    }
    delay(500);
  }

  //stablish barometer
  for (uint8_t i = 0; i < 100; i ++) {    
    BMP180_update();                   
    altitude_hold(2);                                           
    delayMicroseconds(4000);                                                   
  }
  actualPressure = 0; 
#endif

  //check if MS561101BA is ok
#if defined(MS561101BA)
#if DEBUG_STATUS
  Serial.print(F("->CHECKING MS561101BA: "));
#endif

  for (uint8_t i = 0; i < 10; i ++) {
    Wire.beginTransmission(MS5611_ADDRESS);
    uint8_t status = Wire.endTransmission();

    if (status != 0) {
#if DEBUG_STATUS
      Serial.println(F("ERROR"));
#endif
      quadX.status |= QUADX_MS5611_ERROR;
    } else {
#if DEBUG_STATUS
      Serial.println(F("OK"));
#endif      
      MS5611_init();
      quadX.status &= ~QUADX_MS5611_ERROR;
      break;
    }
    delay(500);
  }

#endif

  //wait radio signals 
// #if DEBUG_STATUS  
//   Serial.print(F("->WAITING RADIO SIGNALS: "));
// #endif

//   if (!wait_radio_signals()) {
// #if DEBUG_STATUS
//     Serial.println(F("ERROR"));
// #endif
//     quadX.status |= QUADX_RADIO_STARTUP_FAIL;
//     fail_message();
//   } else {
// #if DEBUG_STATUS
//     Serial.println(F("OK"));
// #endif
//   }

  //bip motors
#if DEBUG_STATUS
  Serial.println(F("->BIP MOTORS"));
#endif

  for (uint16_t i = 0; i < 500; i ++) {
    PORTE |= (1 << PORTE5); PORTB |= (1 << PORTB7);
    PORTH |= (1 << PORTH4); PORTH |= (1 << PORTH6);
    delayMicroseconds(1000);

    PORTE &= ~(1 << PORTE5); PORTB &= ~(1 << PORTB7);
    PORTH &= ~(1 << PORTH4); PORTH &= ~(1 << PORTH6);
    delayMicroseconds(3000);

    seven_seg(0b11000001, 0b10011111, 0b00110001, 0b11111111);
  }

  if (quadX.status & QUADX_EEPROM_READ_FAIL) {
    for (uint8_t i = 0; i < sizeof(fail); i ++) 
      msg[i] = fail[i];
    muxIndex += sizeof(fail);

    for (uint8_t i = muxIndex, k = 0; i < muxIndex + sizeof(eeprom); i ++, k ++) 
      msg[i] = eeprom[k];
    muxIndex += sizeof(eeprom);
  }

  if (quadX.status & QUADX_MPU6050_ERROR) {
    for (uint8_t i = muxIndex, k = 0; i < muxIndex + sizeof(fail); i ++, k ++) 
      msg[i] = fail[k];
    muxIndex += sizeof(fail);

    for (uint8_t i = muxIndex, k = 0; i < muxIndex + sizeof(mpu); i ++, k ++) 
      msg[i] = mpu[k];
    muxIndex += sizeof(mpu);
  }

#if defined(BMP180)
  if (quadX.status & QUADX_BMP180_ERROR) {
    for (uint8_t i = muxIndex, k = 0; i < muxIndex + sizeof(fail); i ++, k ++) 
      msg[i] = fail[k];
    muxIndex += sizeof(fail);

    for (uint8_t i = muxIndex, k = 0; i < muxIndex + sizeof(bmp); i ++, k ++) 
      msg[i] = bmp[k];
    muxIndex += sizeof(bmp);
  }
#endif

#if defined(MS561101BA)
  if (quadX.status & QUADX_MS5611_ERROR) {
    for (uint8_t i = muxIndex, k = 0; i < muxIndex + sizeof(fail); i ++, k ++) 
      msg[i] = fail[k];
    muxIndex += sizeof(fail);

    for (uint8_t i = muxIndex, k = 0; i < muxIndex + sizeof(ms); i ++, k ++) 
      msg[i] = ms[k];
    muxIndex += sizeof(ms);
  }
#endif

  if (quadX.status & QUADX_RADIO_STARTUP_FAIL) {
    for (uint8_t i = muxIndex, k = 0; i < muxIndex + sizeof(fail); i ++, k ++) 
      msg[i] = fail[k];
    muxIndex += sizeof(fail);

    for (uint8_t i = muxIndex, k = 0; i < muxIndex + sizeof(radio); i ++, k ++) 
      msg[i] = radio[k];
    muxIndex += sizeof(radio);
  }

  if (quadX.status & QUADX_ESC_NOT_CALIBRATED) {
    for (uint8_t i = muxIndex, k = 0; i < muxIndex + sizeof(fail); i ++, k ++) 
      msg[i] = fail[k];
    muxIndex += sizeof(fail);

    for (uint8_t i = muxIndex, k = 0; i < muxIndex + sizeof(esc); i ++, k ++) 
      msg[i] = esc[k];
    muxIndex += sizeof(esc);
  }

  if (muxIndex == 0) {
#if DEBUG_STATUS
    Serial.println(F("RESULT: SUCESS"));
#endif
    quadX.status |= QUADX_STATUS_OK;
  } else {
#if DEBUG_STATUS
    Serial.println(F("RESULT: ERROR"));
#endif
  }
  
  quadX.leds |= LED_YELLOW | LED_FRONT | LED_REAR;
}

/*******************************************************
  MPU6050 configuration
/*******************************************************/
void MPU6050_init(void) {
  Wire.beginTransmission(MPU6050_ADDRESS);     
  Wire.write(0x6B); //PWR_MGMT_1
  Wire.write(0x00); //DEVICE_RESET; SLEEP; CYCLE; TEMP_DIS; CLKSEL (00000000, all disable)
  Wire.endTransmission();      

  Wire.beginTransmission(MPU6050_ADDRESS);     
  Wire.write(0x1A); //CONFIG
  Wire.write(0x03); //EXT_SYNC_SET (000, FSYNC input disable); DLPF_CFG (011, ACC bandwidth = 44Hz and GYRO bandwidth = 42Hz)
  Wire.endTransmission();         

  Wire.beginTransmission(MPU6050_ADDRESS);     
  Wire.write(0x1B); //GYRO_CONFIG
  Wire.write(0x08); //XG_ST,YG_ST,ZG_ST (000, disable self test); FS_SEL (1, 01, +- 500°/s [65.5 LSB/°/s] full scale range); ---;
  Wire.endTransmission();  

  Wire.beginTransmission(MPU6050_ADDRESS);     
  Wire.write(0x1C); //ACCEL_CONFIG
  Wire.write(0x10); ///XA_ST,YA_ST,ZA_ST (000, disable self test); AFS_SEL (2, 10, +- 8g [4096 LSB/g] full scale range); ---;
  Wire.endTransmission();                  
}

/*******************************************************
  accelerometer and gyroscope values
/*******************************************************/
bool acc_gyro_values(void) {
  Wire.beginTransmission(MPU6050_ADDRESS);
  Wire.write(0x3B);                      //start reading register 43h and auto increment with every read
  Wire.endTransmission();
  Wire.requestFrom(MPU6050_ADDRESS, 14); //request 14 bytes from the MPU6050

  //reading the low and high bytes of each angle
  if (Wire.available() != 14) return false;

  MPU6050.accX  = (Wire.read() << 8 | Wire.read());      
  MPU6050.accY  = (Wire.read() << 8 | Wire.read());  
  MPU6050.accZ  = (Wire.read() << 8 | Wire.read());     
  MPU6050.temp  = (Wire.read() << 8 | Wire.read());      
  MPU6050.gyroX = (Wire.read() << 8 | Wire.read()); 
  MPU6050.gyroY = (Wire.read() << 8 | Wire.read()); 
  MPU6050.gyroZ = (Wire.read() << 8 | Wire.read()); 

  //invert the direction of the axis
  MPU6050.gyroX *= -1.0;
  MPU6050.gyroY *=  1.0;
  MPU6050.gyroZ *= -1.0;

  //subtract gyroscope calibration value 
  MPU6050.gyroX -= MPU6050.gyroXOffset.val;
  MPU6050.gyroY -= MPU6050.gyroYOffset.val;
  MPU6050.gyroZ -= MPU6050.gyroZOffset.val;

  //subtract accelerometer calibration value
  MPU6050.accX -= MPU6050.accXOffset.val;
  MPU6050.accY -= MPU6050.accYOffset.val;

  return true;
}
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

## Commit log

2023-05-17 add arq
    [1x_Case_bottom.stl, 1x_Case_top.stl, 2x_Battery_holder.stl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]
2023-07-30 execute_pid_controllers->bug in reference signal fixed
    [4x_Skid_landing_gear.stl]
